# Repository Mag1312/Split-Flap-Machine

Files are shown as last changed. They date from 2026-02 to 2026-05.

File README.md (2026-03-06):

# Split-Flap-Machine

This split flap machine is a hobby project by Mag, It is a device which displays time, date, weekday, weather, any word which is less than 7 letters and can even play your favourite songs from a MicroSD Card.

## Introduction

The Split Flap Machine's main attraction, The split flap consists of 37 flaps, 10 numbers (0-9), 26 alphabets (A-Z) and a blank flap. It is made possible mainly with the use of 28byj48 stepper motor, A4988 driver, Hall sensor and an ESP 32. The split flap drum has a small neodimium magnet which gets detected by the hall sensor and sends an update, the place where the magnet's field is not felt by the sensor, is the 0 position. Whenever something is to be displayed, the drum/spool is rotated with respect to this position to display.

The music system works from the webserver, where there are controls to play music. These controls can be used to play music from the MicroSD card.

This all works on a 10000MaH battery.

## Detailed Explanation

The split flap machine consists of 7 split flap units, consisting of 37 flaps, a spool and a stand. A single split flap unit uses a 28byj48 stepper motor, A4988 stepper driver, ky035 hall sensor and a ball bearing.
As mentioned earlier, after the startup a calibration function runs which runs in the following process.

Rotate spool until magnet detected --> Rotate spool until magnet is not detected --> set position = 0

After which to display a character, it first checks the ascii value of the character to be displayed in a seperate array, the position of the array of the ascii value is taken. the position of array times the number of steps per flap is multiplied to get the required position to revolve to display the character. Afterwhich the motor rotates the spool until the position is achieved. There is a killswitch if the spool rotates more than 1 revolution the program fails and freezes.

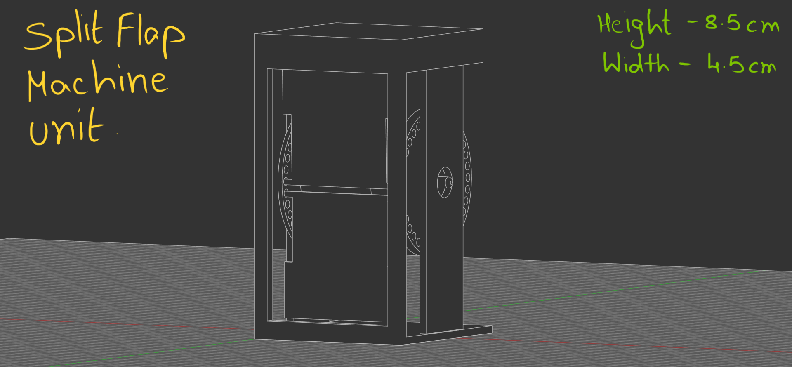
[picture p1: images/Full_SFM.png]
image of a unit of split flap display


You can better understand this in my firmware, go check it out. This is the central operation around which all functions work.

The song system uses a MicroSD card, PCM5102A DAC Module, PAM8406 Amplifier and 2x 8ohm 3Watt speakers. This has been chosen for the highest quality and a mid-high battery life.

The system uses a 10000MaH battery pack with a buck converter to convert voltage.

#

Read Timeline.md for more understanding.

If you have any regards or have found an issue please contact +91 9346651359 (or) email to magazine2512@gmail.com.

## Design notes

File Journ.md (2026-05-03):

---
# Split-Flap-Machine
Author - "Magazine1312/Mag2512/Mag1312"
Descrption - "A Split Flap Machine is a device worthy to display 7 letter words, Weather, Clock, Day, Date etc.. It can even play Music!"
Created - "2026-02-25"
This file focuses on the process of creation of Split Flap Machine as created by Mag (The creator)
---

[Note - The measurements are not mentioned unless specified in the timeline text, It is expected that the reader will download the files to check the measurements]

# Febrauary 25: Created Spool and Flaps for Machine

Created the flaps (Self Explanatory)
Created the Spools (The drums where the flaps are placed for SFM to rotate)
 - The spool has been divided into 2 parts, The part 1 (The top part) and part 2 (The bottom part) [look at the image for better understanding]

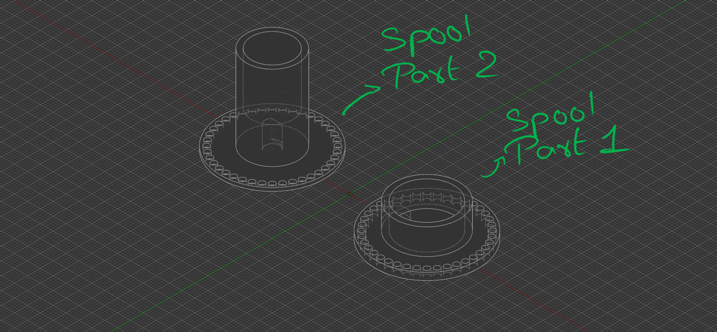
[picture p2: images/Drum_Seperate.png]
Spools


Both the spools have 40 holes, having diameter greater than that of flap ends. The angle between the centres of two circles and the centre of the base of the spool is 9 degrees.

The spools are attached to eachother by inserting Spool 2 into Spool 1. For better understanding, please refer to the image below.

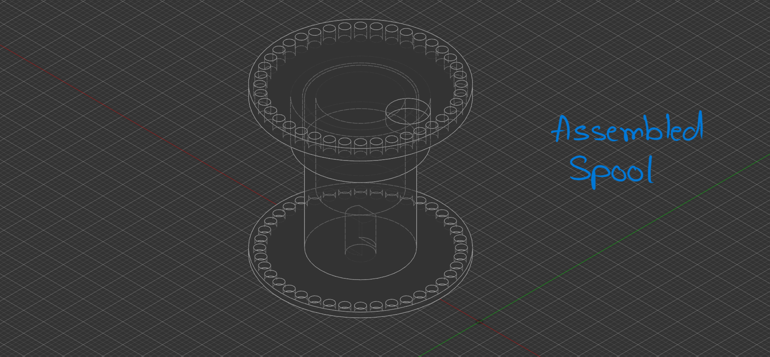
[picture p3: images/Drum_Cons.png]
Image of a constructed spool


The spool 1 has a cavity for holding a Neodymium magnet for the working of Hall sensor which is specified later.
Simillarly spool 2 has a cavity for the Stepper motor's shaft to rotate the spool also specified later.

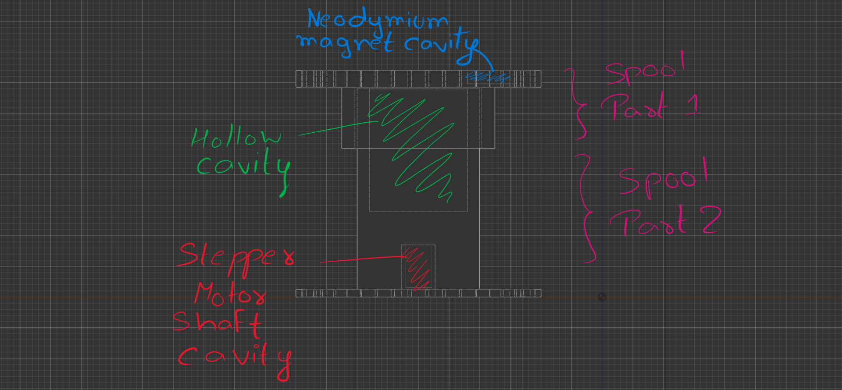
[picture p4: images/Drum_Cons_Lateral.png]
Image of a constructed spool's lateral section


The semi constructed spool with flap is given below, for complexity and space constraints only one flap has been attached.

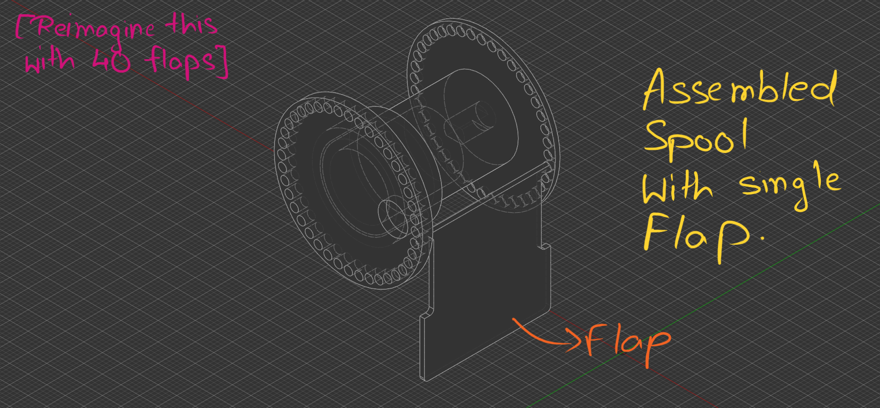
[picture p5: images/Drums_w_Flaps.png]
Image of a constructed spool with a flap attached


**Total Time Spent: 4 hours**

# February 26: Created Spool Holder and updated designs

Created a Spool stand. SPECIFICALLY designed for when the flaps of the spool hit the front part of the stand, it doesnt fall and stays there until there is a 10 degree rotation.

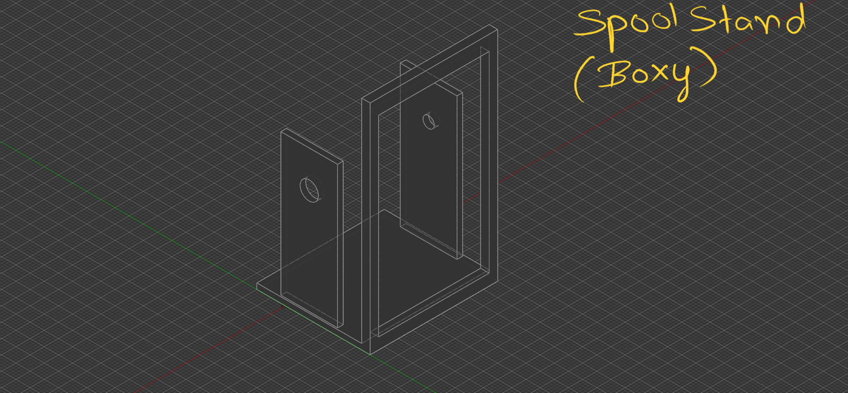
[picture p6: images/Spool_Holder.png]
Image of spool stand


And we got some changes, Since The older spool design with 40 holder was TOO EXPENSIVE (The cost adds up for 7 of them, so its 280 if its 40 holders) so I reduced it to only 36. 26 for letters and 10 for numbers from 0-9.

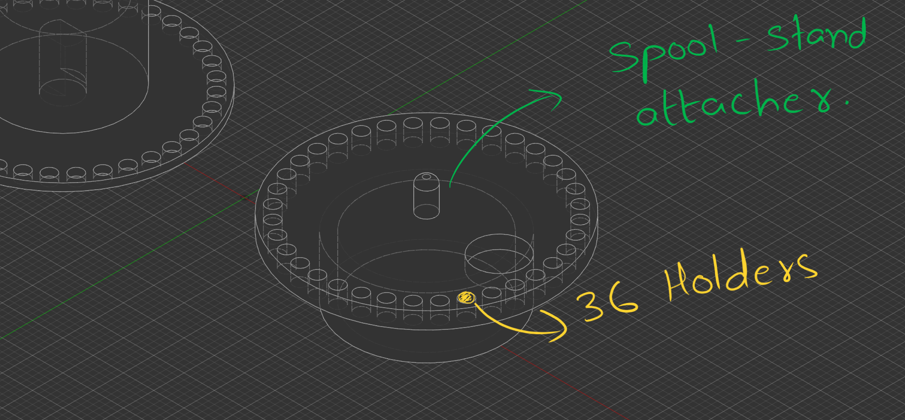
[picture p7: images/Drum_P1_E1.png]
Image of updated spool V1


Here you can see the spool stand attacher, ensuring that it can rotate freely without disorientating.

Welp, its 2am and I've made some changes. 
The spool stand attacher will work however for smooth rotation I have decided to use ball bearings of 3x8x4mm. I had to do multiple revisions and changes for the somewhat final SFM unit.
firstly I added a cavity for ball bearing as mentioned. Next I made the height of the SFM unit around 8.5cm and also had to add an offset slab which stops the top flap from falling down unless turned 10 degress. (See the image)
and next I updated the overall look of the Stand it looks more boxier and it was the design I was going for.

1.5 hrs of work

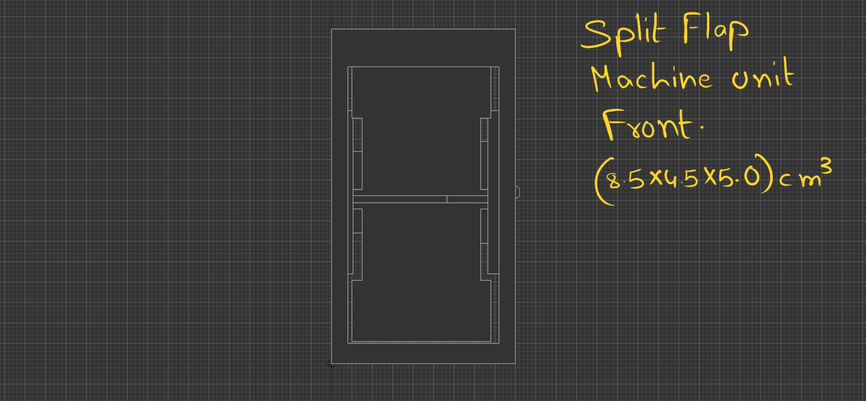
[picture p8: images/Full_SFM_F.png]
another one


**Total Time Spent: 3 hours**

# February 27: Updated Spool Stand Design and made a BOM list

As soon as I woke up I made a cavity in the Spool Holder for a screw so that when the flaps fall they make the sound which we want to hear and also makes the flaps not swing after falling down (This is the major cause).

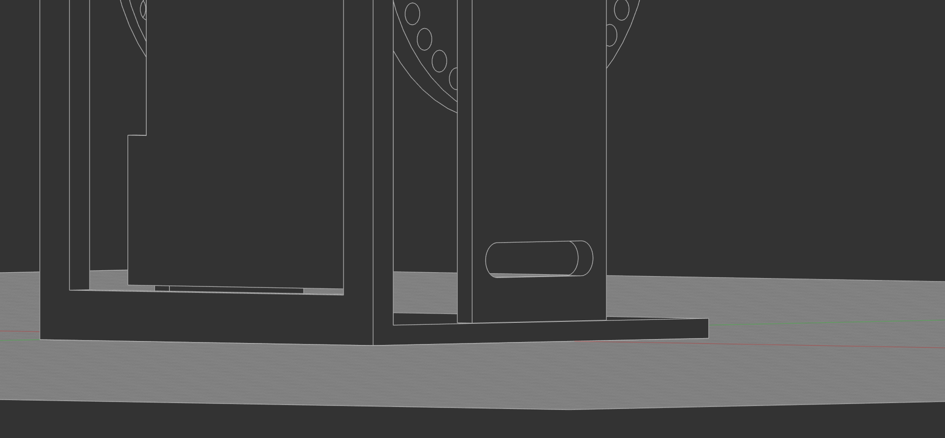
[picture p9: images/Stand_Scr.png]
Spool Stand Screw Cavity


Next Since the design was nearly final I made a BOM list although I Have not decided yet how to power this so I have not included any power supply or things which are used to power this (I have to Research). And the total cost of the machine comes to nearly 97$, A whole lot of expensive, Major cost includes 3d printing service, filament and Arduino Nano. Well 3d printing in my local is much cheaper than online service which is charging, 110$ JUST FOR THE FLAPS OF 7 UNITS! In the price of flaps I can print my whole machine locally, However I doubt blueprint will give me funds to convert credit into real money so I can pay the local service so I doubt it.

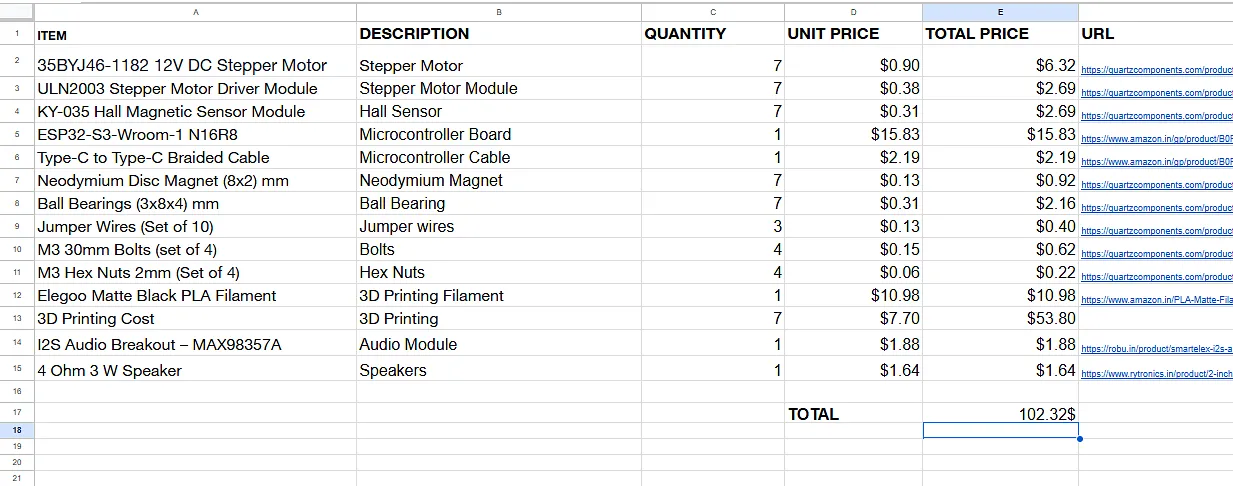
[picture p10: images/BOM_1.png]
BOM


**Total Time Spent: 3 hours**

# March 1: Made code to calibrate the machine

This day was brainfoggy one, I had no idea how to code the script and I had to go through multiple videos of how arduino's control stepper motors, haul sensor and in basic the whole setup (the code is same for arduino and esp32). Even after all this, I was still not able to find what to do so I asked chatGPT and it asked me to follow a path. I had the map and was on my own, testing logics and all. I worked on calibration today, What it does is that everytime the SFM starts up, it doesnt know which letter it is displaying so in the calibration it slowly rotates the spool and uses the hall sensor to detect the magnet, when the magnet is in close contact to the hall sensor the hall sensor reads LOW and vice versa. So this calibration is only right when the hall sensor first reads HIGH then LOW then HIGH and the point where hall sensor transitions from LOW to HIGH is the point of 0 position and all characters are labelled relative to this position.

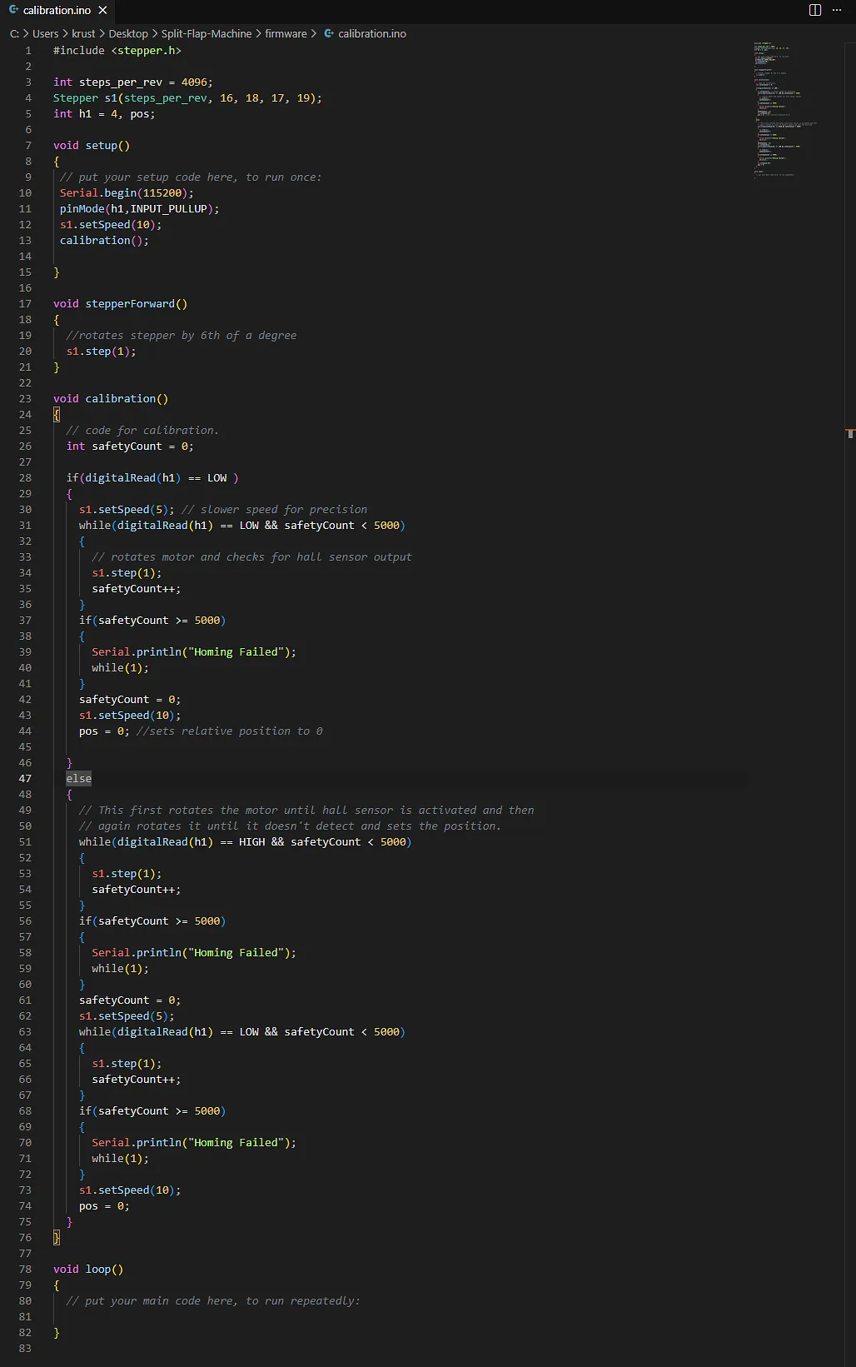
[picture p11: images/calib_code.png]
code of calibration


**Total Time Spent: 4 hours**

# March 4: Made code to connect ESP 32 to the internet to get data like time

Today I made a code to fetch time from the internet (watch this video for info : https://youtu.be/9OcewS8sa68?si=-juCJv46duffQA7_). And I also updated the BOM list because with only 1 esp 32, I would be falling short of gpio pins for the motors and other features, So I had two options either use a gpio extension board or buy another esp 32. After painfully reading the advantages and disadvantages of both, it was quite clear that another esp 32 is the best option so I did  so!

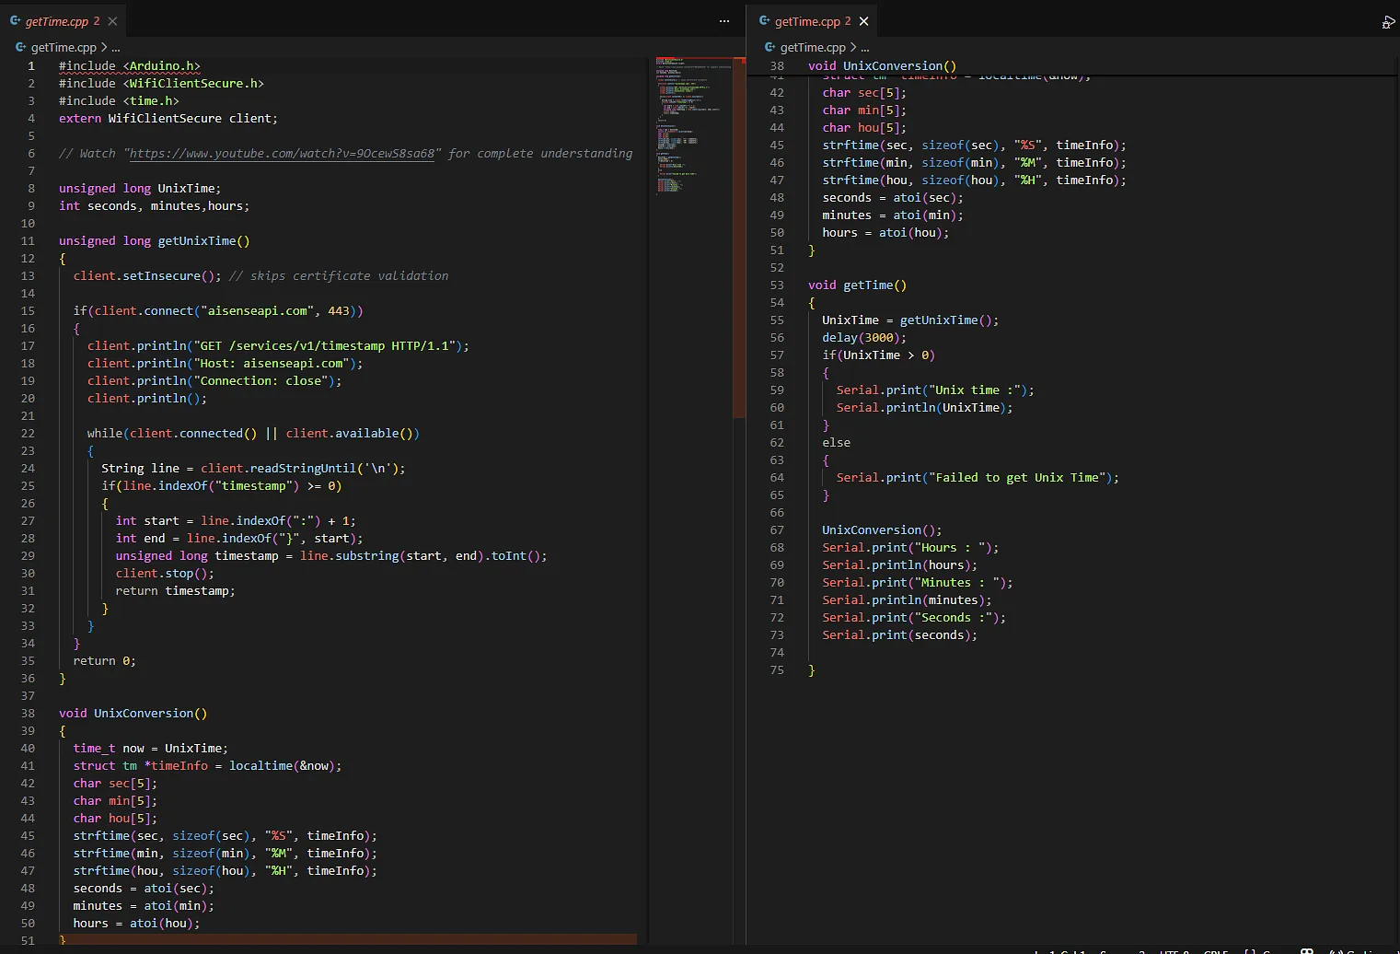
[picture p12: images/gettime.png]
code of getTime function


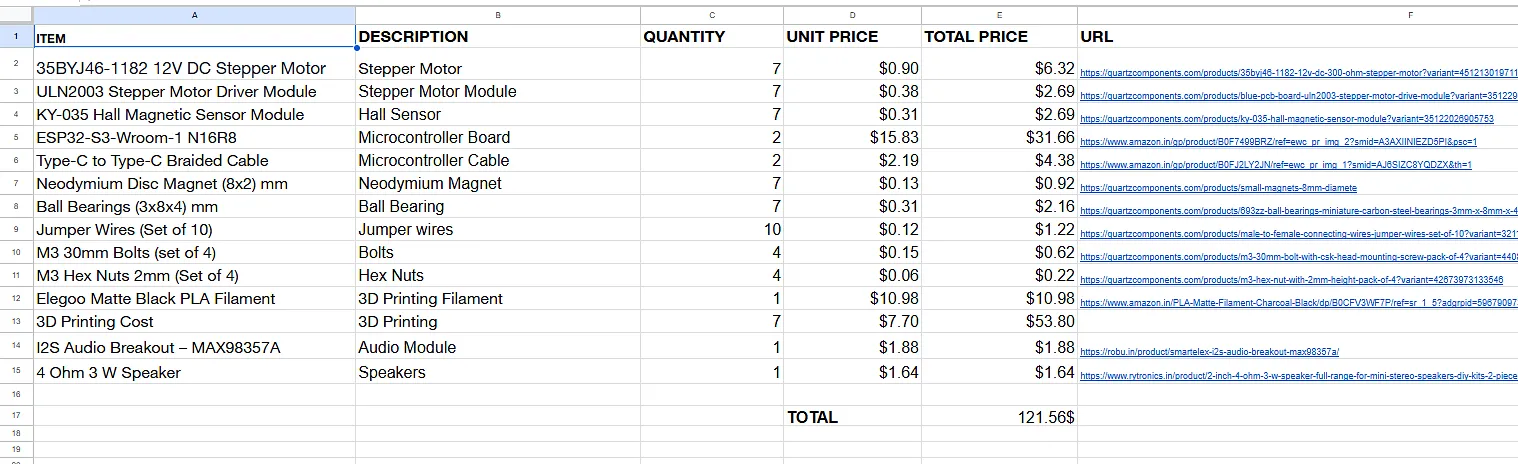
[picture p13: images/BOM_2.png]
BOM LIST 2


**Total Time Spent: 5 hours**

# March 5: I made code to calibrate all units at once

In todays episode of Split Flap Device, I made a code for all the 7 units of the device to calibrate at once!

This is achieved by calling the setupCalibration() function from the main .ide file. This function then called the fullCalibration() function.

Here's a simple explanation of the full calibration function - First the hall sensors output is detected if it is on the magnet or near its magnetic field, it goes in the first if block, in it one motor is rotated by 1 step and then it is checked if the hall sensors output has changed, if not it goes to the setupCalibration() function and in the loop follows fullCalibration() function again for another stepper motor.

This process might seem lengthy but to the human eye it seems as if all the 7 units are being calibrated at once! The delay between 2 fullCalibration() functions is so small that it is not noticable!

Props to Chatgpt for letting me know this process, It was quite interesting and very understandable and I was able to code without any help of chatGPT using my own skills!

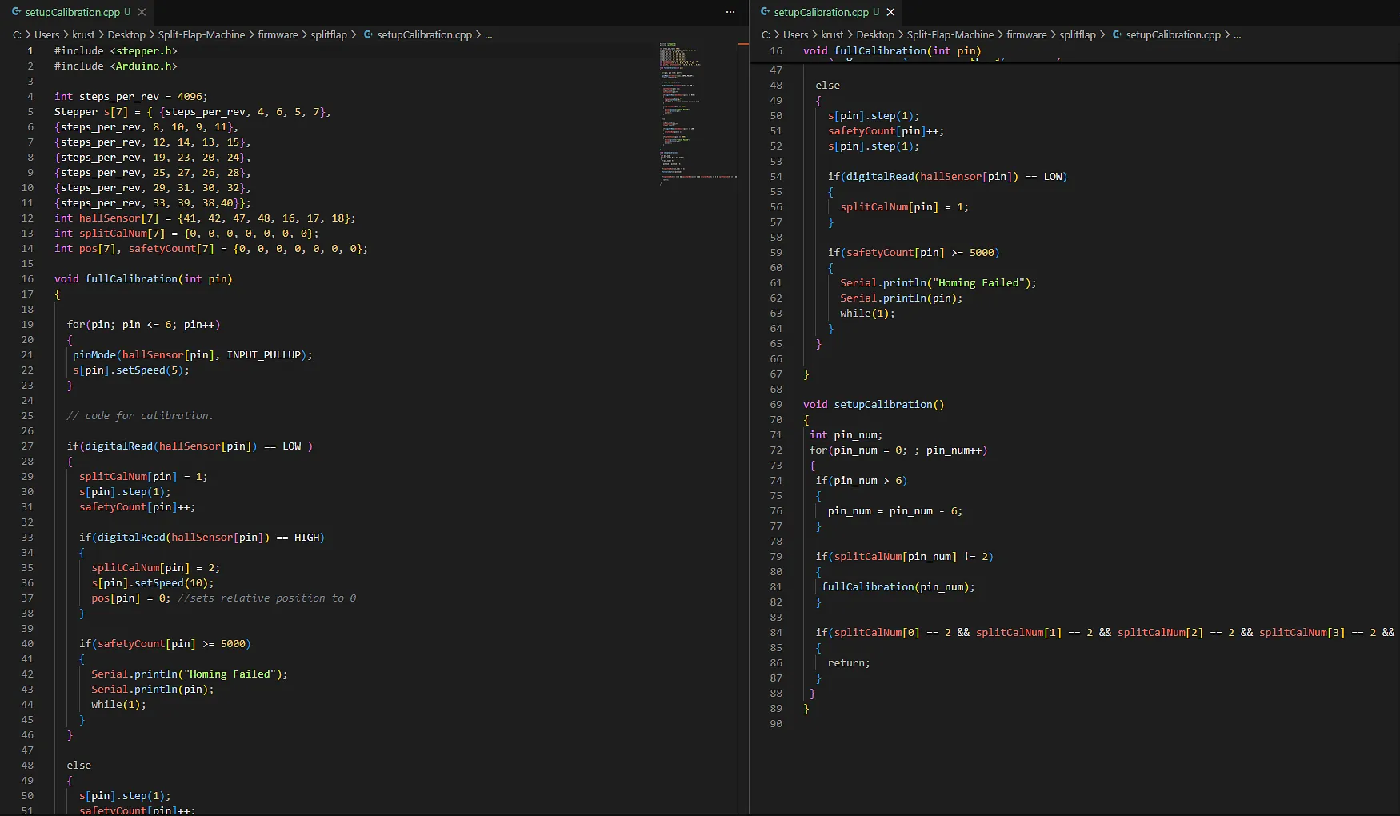
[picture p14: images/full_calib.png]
code of full calibration


**Total Time Spent: 4 hours**

# March 6: Made code to display Time, Date, Weather, Day

This was one of the most productive days.

Today I made a program to display time, date, weather, weekday on my split flap device!

Inshort today was a day of arduino ide, It took a lot of time, approximately 6 hours for all these but it was worth it!

the displaying works on the following principle -
It first arranges the words to be displayed in a character array and compares it with ascii values, if it matches it goes on an gets a position which is calculated so that only that letters position is sent. Next the motors rotate one by one by 1 step until all of they reach their final position.

This is the basic program and is used in all 4 of my programs. The weather program however uses api to get its data from the internet through esp 32s wifi feature.

Thats it for today, tommorrows plan is to make a webserver for esp32 and make a program so that when a word is entered in the webserver it is displayed on the split flap machine.

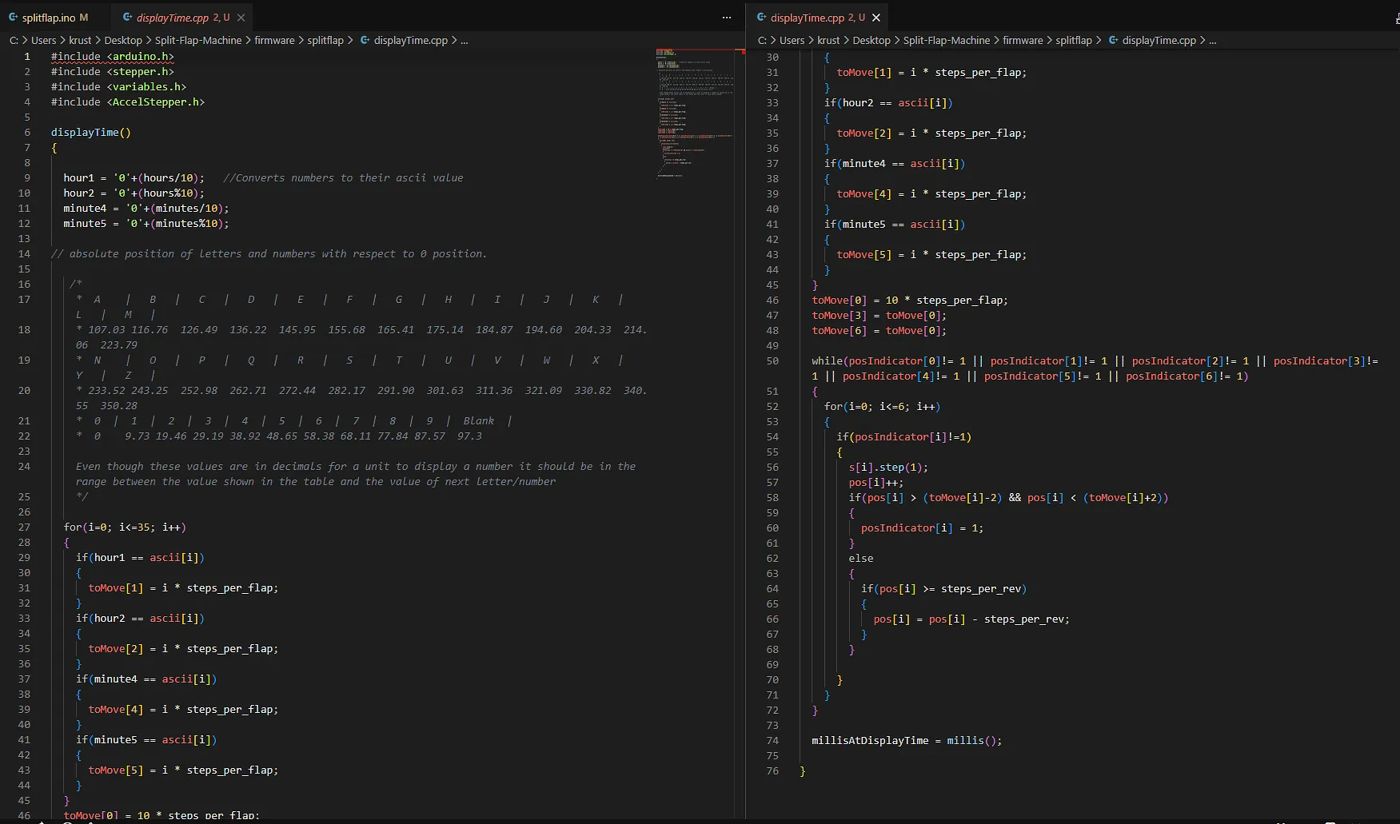
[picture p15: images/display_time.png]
code of display time


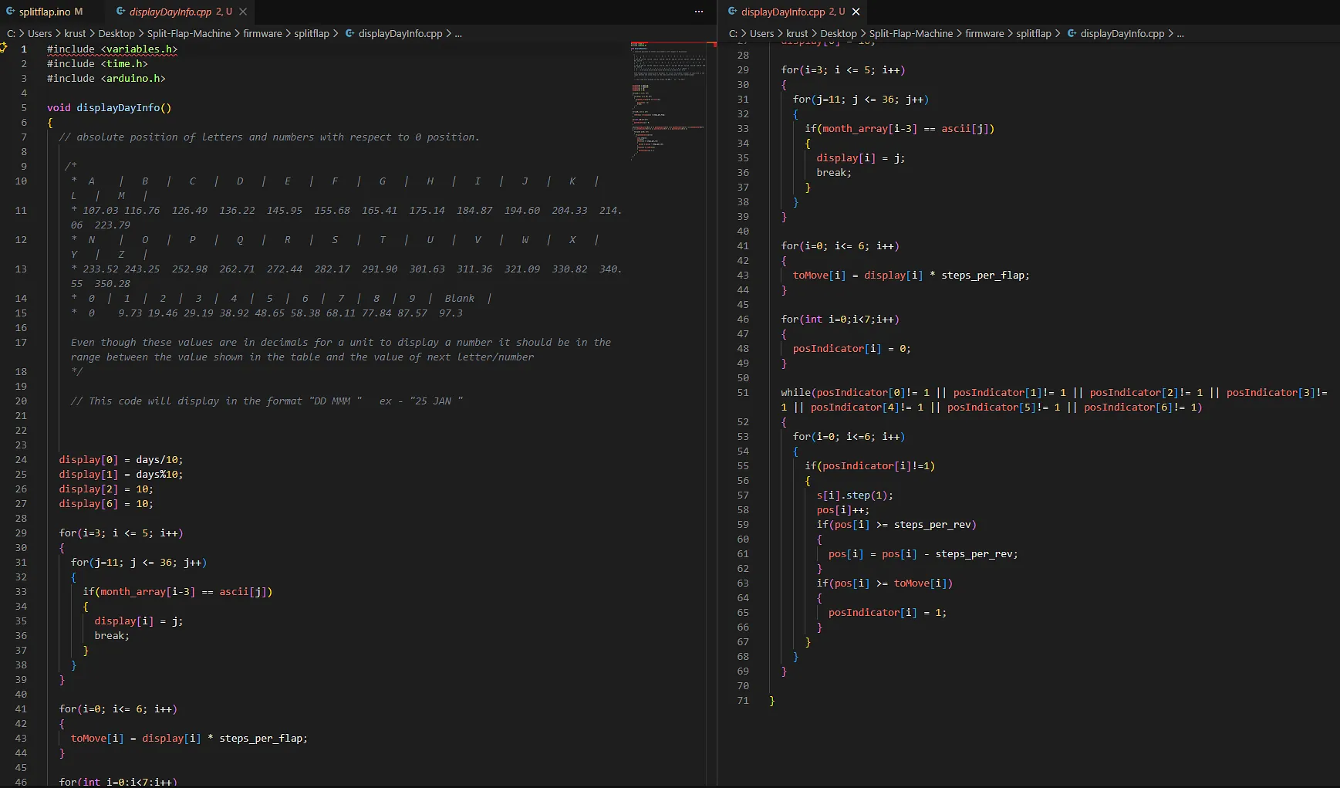
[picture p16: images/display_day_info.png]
code of display date


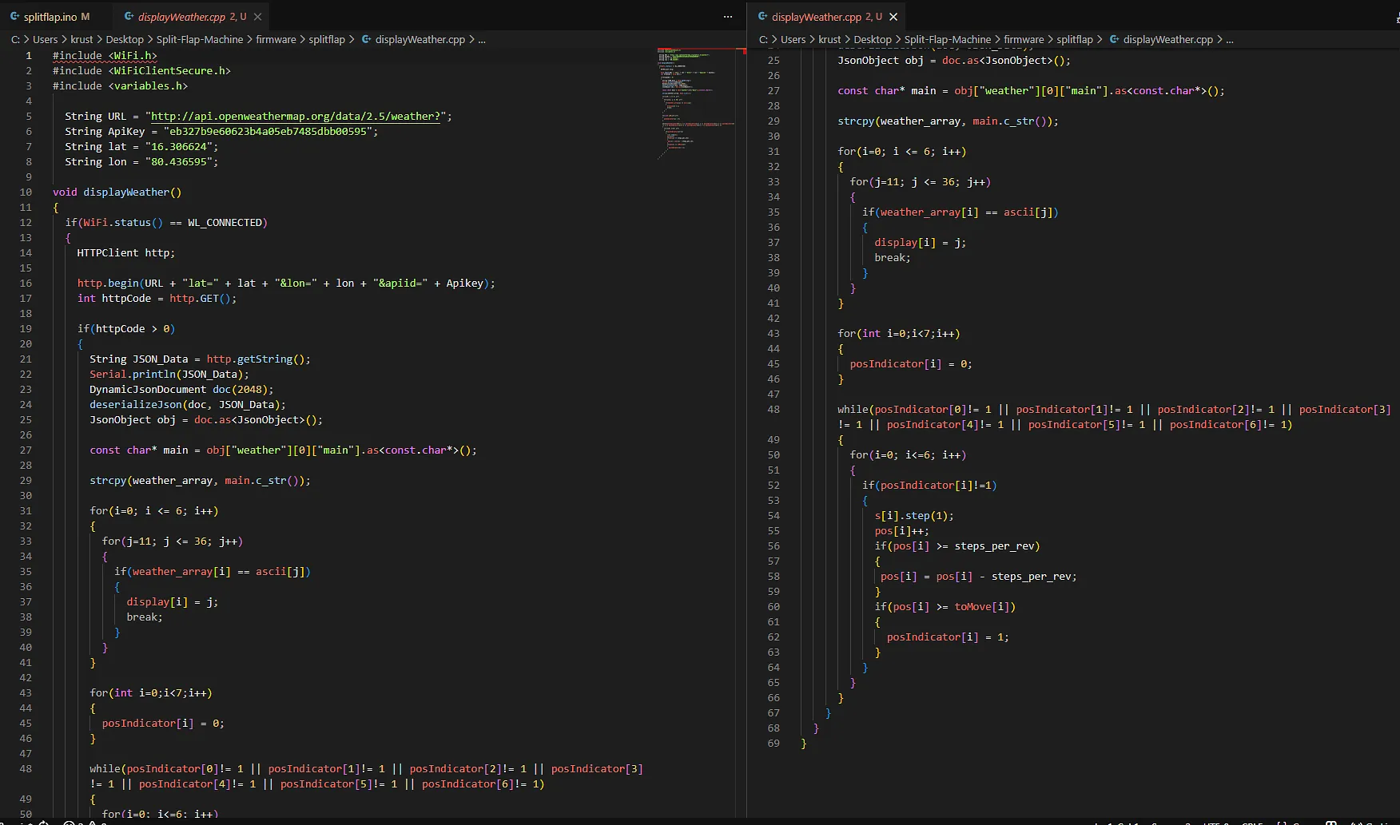
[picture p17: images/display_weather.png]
code of display weather


**Total Time Spent: 6 hours**

# March 7: Completed the software part and made a final BOM list

Today was the day where the software part was completed!

In todays episode of Split Flap Display, I created a webserver having the functionality so that one can control the split flap machine from their phone, It also has song playback feature. This is achieved through UART communication between 2 ESP32s, which uses an MicroSD card to store all the songs. 

This could be updated to a streaming playback in the future, which is a matter of only few code lines.

I also updated the final BOM list for Hackclub's design review and funds allocation.

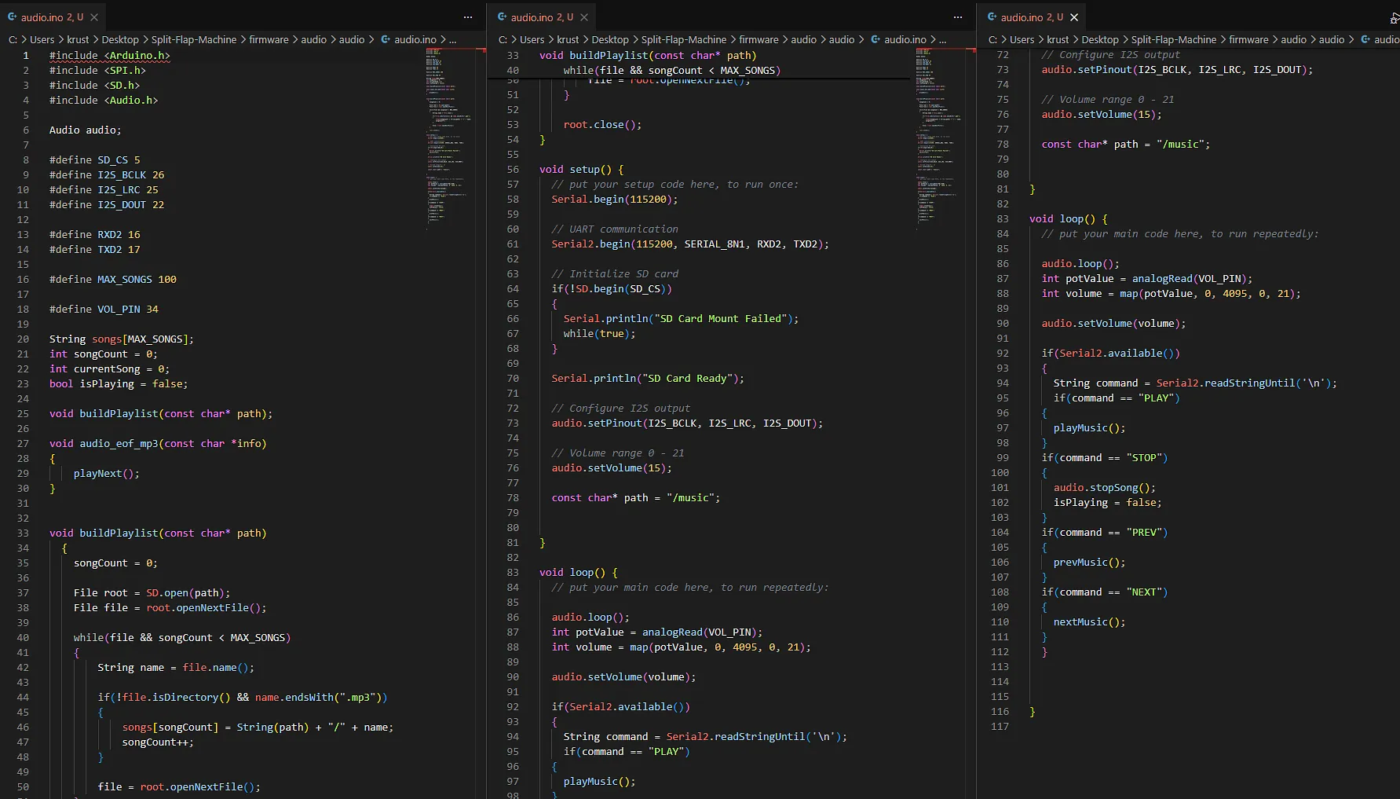
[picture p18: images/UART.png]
code of audio


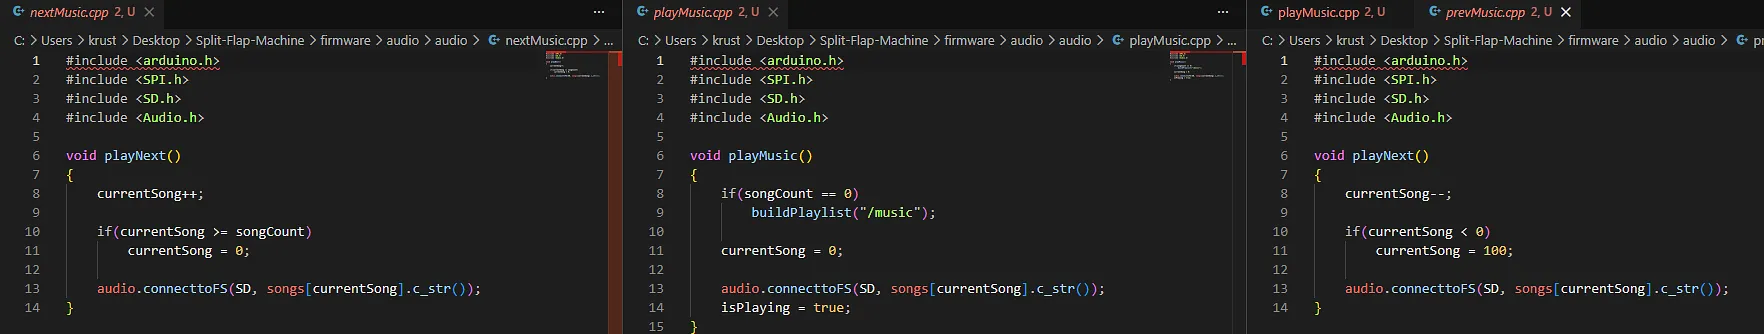
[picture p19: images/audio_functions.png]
code of audio2


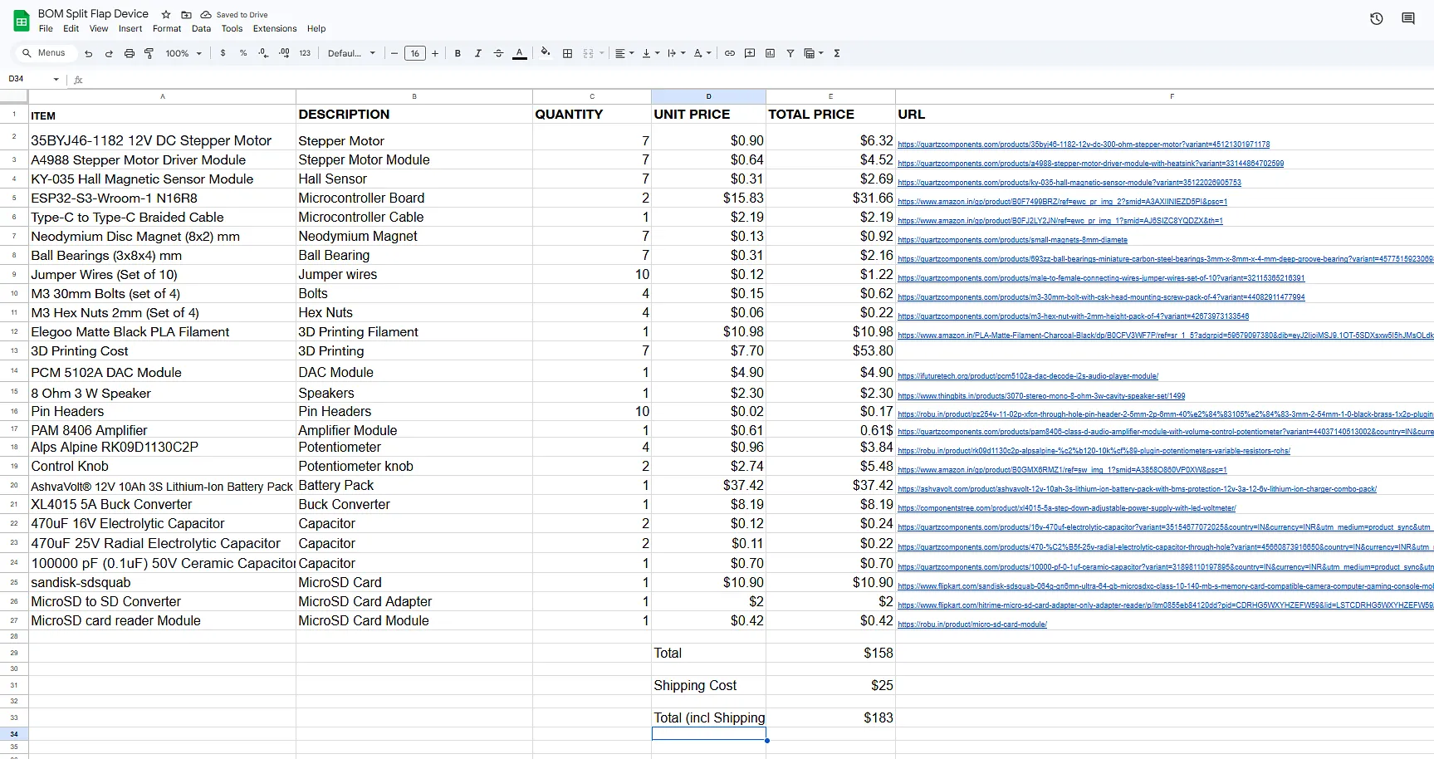
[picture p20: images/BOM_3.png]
BOM LIST


And Hence today I submit the design review and hopefully it goes clear.

**Total Time Spent: 6 hours**

#

**Time Spent on Project: 35 hours**

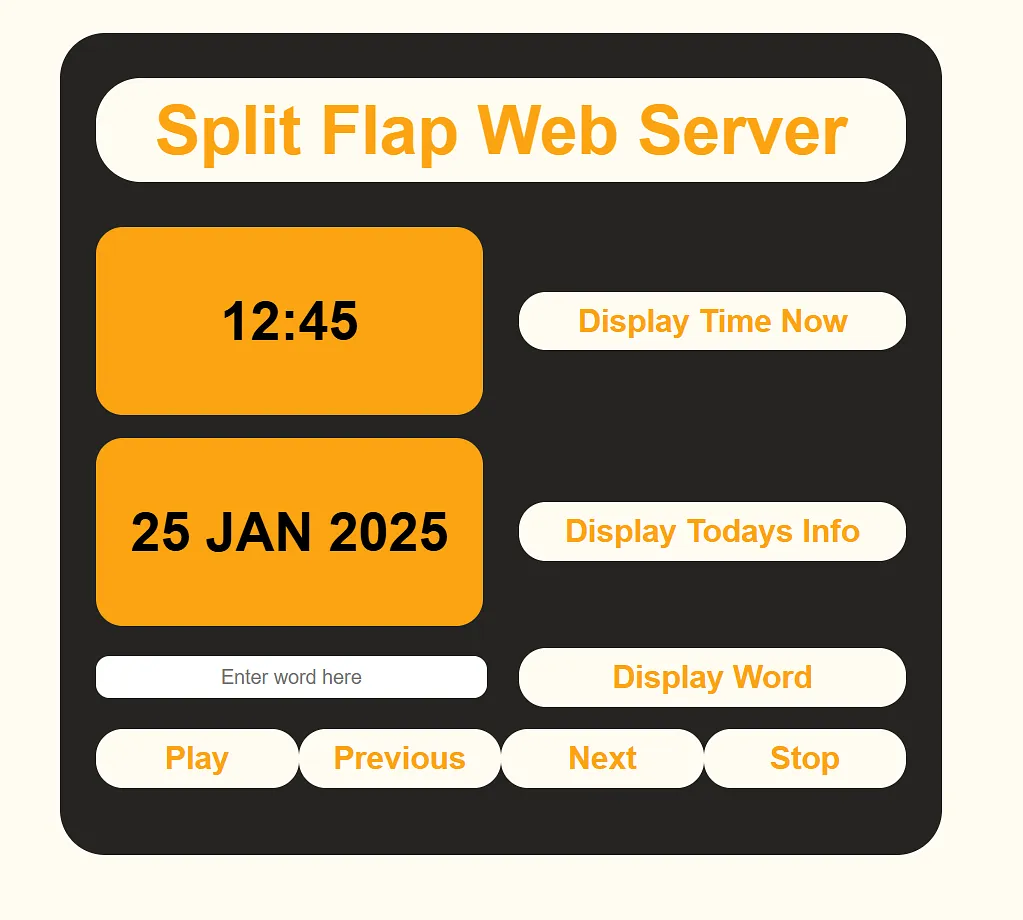
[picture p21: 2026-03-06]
images/Web_server.png

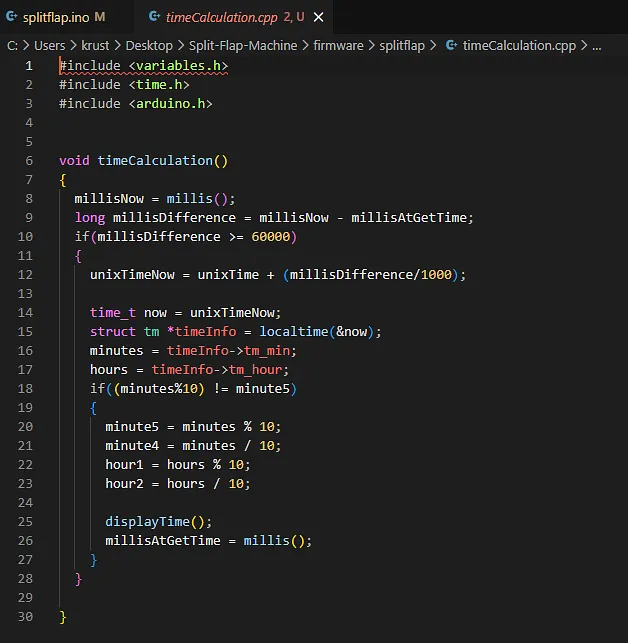
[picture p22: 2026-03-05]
images/time_calculation.png

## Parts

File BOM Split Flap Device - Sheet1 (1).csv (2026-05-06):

ITEMS | DESCRIPTION | QUANTITY | UNIT PRICE | TOTAL PRICE | URL | OTHER INFO
28BYJ48 5V DC Stepper Motor | Stepper Motor | 7 | $0.97 | $6.70 | https://robu.in/product/28byj-48-stepper-motor-dc-5v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
A4988 Stepper Motor Driver Module | Stepper Motor Module | 7 | $0.76 | $5.34 | https://quartzcomponents.com/products/a4988-stepper-motor-driver-module-with-heatsink?variant=33144864702599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
KY-035 Hall Magnetic Sensor Module | Hall Sensor | 7 | $0.21 | $1.48 | https://quartzcomponents.com/products/ky003-hall-effect-magnetic-sensor?variant=39261093134520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
ESP32-S3-Wroom-1 N16R8 | Microcontroller Board | 2 | $10.58 | $21.16 | https://www.amazon.in/LAND-INDIA-ESP32-Development-Microcontroller/dp/B0FG3BBKPH
Type-C to Type-C Braided Cable | Microcontroller Cable | 1 | $2.19 | $2.19 | https://www.amazon.in/gp/product/B0FJ2LY2JN/ref=ewc_pr_img_1?smid=AJ6SIZC8YQDZX&th=1
Neodymium Disc Magnet (8x2) mm | Neodymium Magnet | 7 | $4.52 | $4.52 | https://www.flipkart.com/jinsa-50pcs-dia-8x2mm-round-disc-neodymium-rare-earth-magents-art-crafts-multipurpose-office-magnets-pack-50/p/itm078c0c0845b31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
Ball Bearings (3x8x4) mm | Ball Bearing | 7 | $0.31 | $2.16 | https://quartzcomponents.com/products/693zz-ball-bearings-miniature-carbon-steel-bearings-3mm-x-8mm-x-4-mm-deep-groove-bearing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
M3 30mm Bolts (set of 4) | Bolts | 4 | $0.15 | $0.62 | https://quartzcomponents.com/products/m3-30mm-bolt-with-csk-head-mounting-screw-pack-of-4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
M3 Hex Nuts 2mm (Set of 4) | Hex Nuts | 4 | $0.06 | $0.22 | https://quartzcomponents.com/products/m3-hex-nut-with-2mm-height-pack-of-4?variant=42673973133546
Female Headers (2 pin) | Pin Headers | 50 | $0.08 | $4.21 | https://robu.in/product/fh1-27-01-02pzd-xunpu-plugin1x2-pin-1-27mm-female-headers-rohs/
Female Headers (3 pin) | Pin Headers | 10 | $0.08 | $0.90 | https://robu.in/product/fh1-0-01-03pzd-xunpu-plugin1x3-pin-1mm-female-headers-rohs/
PCM 5102A DAC Module | DAC Module | 1 | $4.90 | $4.90 | https://ifuturetech.org/product/pcm5102a-dac-decode-i2s-audio-player-module/
8 Ohm 5 W Speaker | Speakers | 1 | $3.16 | $3.16 | https://thinkrobotics.com/products/2030-cavity-speaker-8%CF%89-2w?variant=49309283025213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
Pin Headers | Pin Headers | 10 | $0.02 | $0.17 | https://robu.in/product/pz254v-11-02p-xfcn-through-hole-pin-header-2-5mm-2p-6mm-40%e2%84%83105%e2%84%83-3mm-2-54mm-1-0-black-brass-1x2p-pluginp2-54mm-pin-head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
PAM 8406 Amplifier | Amplifier Module | 1 | $0.61 | 0.61$ | https://quartzcomponents.com/products/pam8406-class-d-audio-amplifier-module-with-volume-control-potentiometer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
Alps Alpine RK09D1130C2P | Potentiometer | 4 | $0.96 | $3.84 | https://robu.in/product/rk09d1130c2p-alpsalpine-%c2%b120-10k%cf%89-plugin-potentiometers-variable-resistors-rohs/
Control Knob | Potentiometer knob | 2 | $2.74 | $5.48 | https://www.amazon.in/gp/product/B0GMX6RMZ1/ref=sw_img_1?smid=A3858O860VP0XW&psc=1
AshvaVolt® 12V 10Ah 3S Lithium-Ion Battery Pack | Battery Pack | 1 | $37.42 | $37.42 | https://ashvavolt.com/product/ashvavolt-12v-10ah-3s-lithium-ion-battery-pack-with-bms-protection-12v-3a-12-6v-lithium-ion-charger-combo-pack/
XL4015 5A Buck Converter | Buck Converter | 1 | $7.89 | $7.89 | https://robu.in/product/xl4015-5a-dc-dc-step-adjustable-power-supply-buck-module-led-w-voltmeter/?gad_source=1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
0.1uF Ceramic Capacitor | Capacitor | 30 | $0.06 | $1.91 | https://quartzcomponents.com/products/10000-pf-0-1uf-ceramic-capacitor?variant=31898110197895
470uF 50V Electrolytic Capacitor | Capacitor | 1 | $0.07 | $0.07 | https://quartzcomponents.com/products/470uf-50v-electrolytic-capacitor
47uF 10V Electrolytic Capacitor | Capacitor | 2 | $0.04 | $0.08 | https://quartzcomponents.com/products/47uf-10v-electrolytic-capacitor
100uF 16V Electrolytic Capacitor | Capacitor | 10 | $0.03 | $0.35 | https://quartzcomponents.com/products/6v-100uf-electrolytic-capacitor
100uF 25V Electrolytic Capacitor | Capacitor | 10 | $0.03 | $0.35 | https://quartzcomponents.com/products/100uf-25v-radial-electrolytic-capacitor
1000uF 16V Electrolytic Capacitor | Capacitor | 2 | $0.08 | $0.20 | https://quartzcomponents.com/products/1000uf-16v-aluminum-electrolytic-capacitors-leaded
sandisk-sdsquab | MicroSD Card | 1 | $16.83 | $16.83 | https://www.flipkart.com/sandisk-sdsquab-064g-gn6mn-ultra-64-gb-microsdxc-class-10-140-mb-s-memory-card-compatible-camera-computer-gaming-console-mobile-table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
MicroSD to SD Converter | MicroSD Card Adapter | 1 | $3 | $3 | https://www.flipkart.com/carecase-pack-3-sam-sung-micro-sd-adapter-compatible-all-mobile-memory-cards-card-reader/p/itmc5f69c3882c43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
MicroSD card reader Module | MicroSD Card Module | 1 | $0.42 | $0.42 | https://robu.in/product/micro-sd-card-module/
9x15cm Perf Board | Perf Board (PCB) | 2 | $0.98 | $2 | https://robu.in/product/9-x-15-cm-universal-pcb-prototype-board-single-sided-2-54mm-hole-pitch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
4x6cm Perf Board | Perf Board (PCB) | 1 | $1 | $1 | https://robu.in/product/5-x-7-cm-universal-pcb-prototype-board-single-sided-2-54mm-hole-pitch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
Pin Headers (2 Pin) | Pin Headers | 30 | $0.03 | $1 | https://robu.in/product/ph1-0-01-02pzd-xunpu-plugin1x2-pin-1mm-pin-headers-rohs/
Pin Headers (3 Pin) | Pin Headers | 10 | $0.03 | $1 | https://robu.in/product/ph1-27-01-03pzd-xunpu-plugin1x3-pin-1-27mm-pin-headers-rohs/
Jumper Wires (20 cm) | Jumper Wires | 1 | $0.46 | $0.46 | https://robu.in/product/male-to-female-jumper-wires-40pcs-20cm/
18AWG (RED) | Wires | 1 | $0.34 | $0.34 | https://robu.in/product/18awg-high-voltage-silicone-wire-3000v-red/
18AWG (BLACK) | Wires | 1 | $0.34 | $0.34 | https://robu.in/product/18awg-high-voltage-silicone-wire-3000v-black/
20AWG (RED) | Wires | 2 | $0.16 | $0.32 | https://robu.in/product/ul1007-20awg-pvc-electronic-wire-red/
20AWG (BLACK) | Wires | 2 | $0.16 | $0.32 | https://robu.in/product/ul1007-20awg-pvc-electronic-wire-black/
22AWG (RED) | Wires | 2 | $0.16 | $0.32 | https://robu.in/product/22awg-silicone-braided-wire-red/
22AWG (BLACK) | Wires | 2 | $0.16 | $0.32 | https://robu.in/product/22awg-silicone-braided-wire-black/
26AWG (RED) | Wires | 2 | $0.08 | $0.16 | https://robu.in/product/high-quality-ultra-flexible-26awg-silicone-wire-1000m-red/
26AWG (BLACK) | Wires | 2 | $0.08 | $0.16 | https://robu.in/product/ul1007-26awg-pvc-electronic-wire-black/
Wire Stripper | Wire Stripper | 1 | $2.55 | $2.55 | https://robu.in/product/multitec-02dx-self-adjusting-wire-cutter-stripper/
Helping Hands | Helping Hands | 1 | $9.40 | $9.40 | https://www.amazon.in/gp/product/B0DFQ6G523/ref=ewc_pr_img_1?smid=A3T8K809Q96RB6&psc=1
Solder Wick | Solder Wick | 1 | $0.70 | $0.70 | https://robu.in/product/best-quality-solder-desoldering-wire-de-soldering-wick/
 |  |  | TOTAL - | $156.23
 |  |  | TOTAL (incl Shipping) - | $180

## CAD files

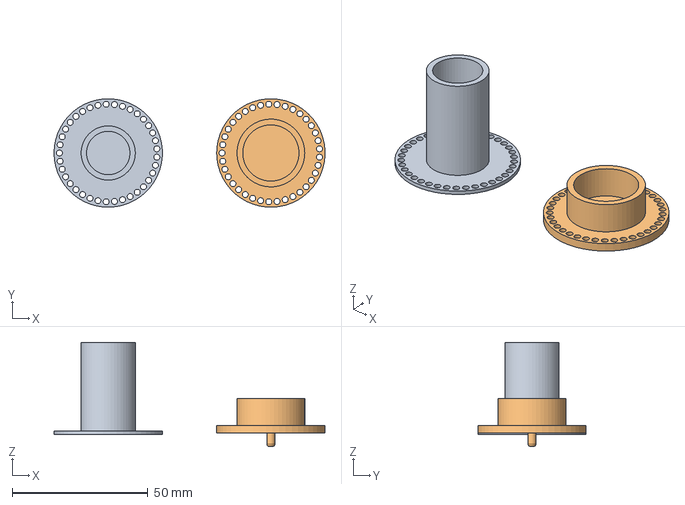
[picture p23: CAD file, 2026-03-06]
CAD STEP/Drum.stp
100.0 x 40.0 x 38.5 mm

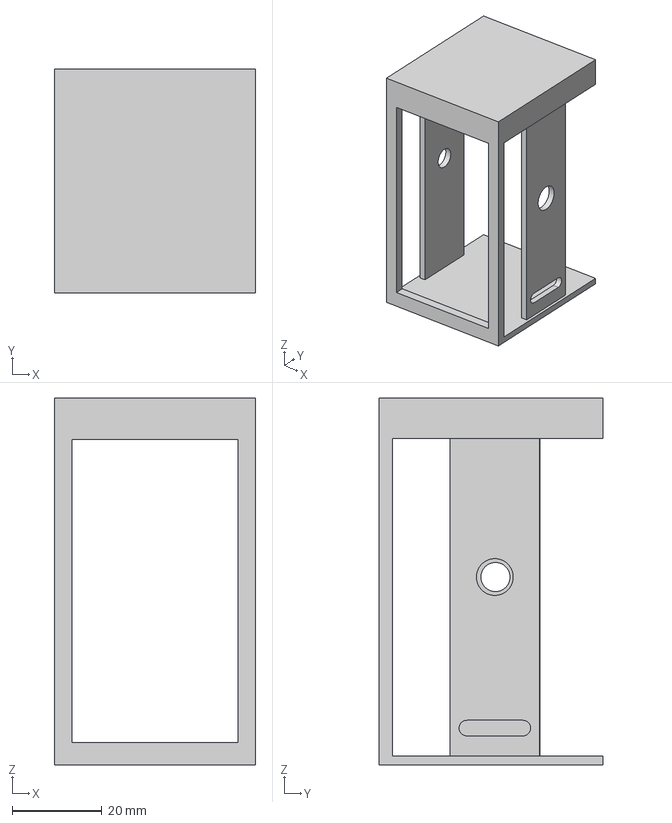
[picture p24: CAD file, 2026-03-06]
CAD STEP/Spool+Stand.stp
45.0 x 50.0 x 82.0 mm

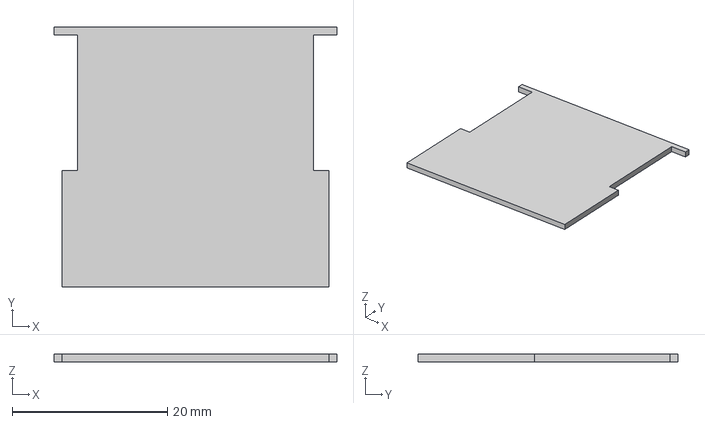
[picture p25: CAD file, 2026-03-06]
CAD STEP/Flaps.stp
36.5 x 33.5 x 1.00 mm

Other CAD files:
CAD/Drum.f3d
CAD/Flaps.f3d
CAD/Spool Stand.f3d

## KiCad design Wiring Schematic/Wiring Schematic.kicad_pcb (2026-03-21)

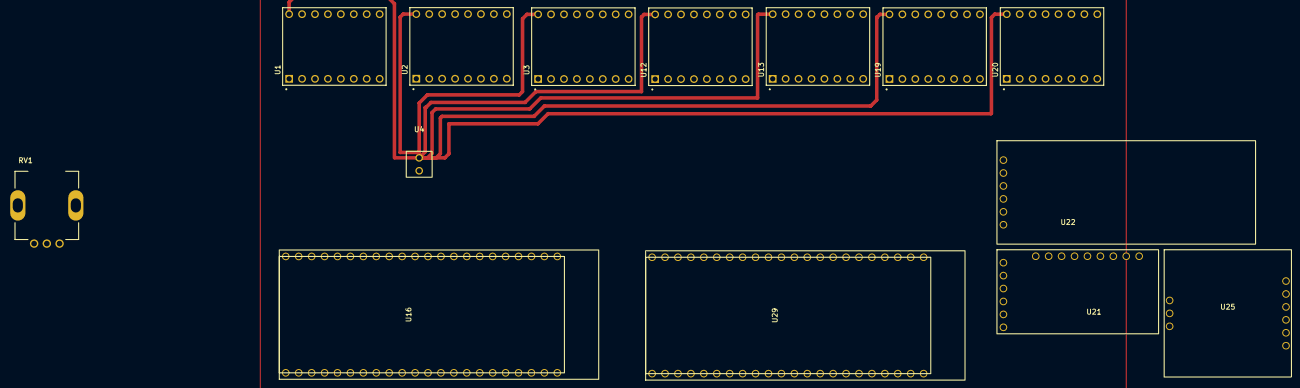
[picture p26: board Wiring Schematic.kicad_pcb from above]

Board: 2 copper layers, 14 parts (0 on the bottom side), 29 nets.

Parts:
RV1: R_Potentiometer; XDCR_PEC11R-4215F-S0024
U1, U2, U3, U12, U13, U19, U20: MODULE_A4988_STEPPER_MOTOR_DRIVER_CARRIER
U4: Buck_Converter
U16, U29: ESP 32 S3 Devkit C1
U21: PCM5102A_DAC
U22: MicroSD_Module
U25: PAM_8406

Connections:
+3.3V: RV1.3, U1.RST (RESET), U1.VDD, U2.RST (RESET), U2.VDD, U3.RST (RESET), U3.VDD, U12.RST (RESET), U12.VDD, U13.RST (RESET), U13.VDD, U16.3V3, U19.RST (RESET), U19.VDD, U20.RST (RESET), U20.VDD, U21.VIN, U22.VCC, U29.3V3
+5V: U1.VMOT, U2.VMOT, U3.VMOT, U4.P_OUT(+), U12.VMOT, U13.VMOT, U16.5V (5V0), U19.VMOT, U20.VMOT, U25.VCC, U29.5V (5V0)
GND: RV1.1, U1.MS1, U1.MS2, U1.MS3, U2.MS1, U2.MS2, U2.MS3, U3.MS1, U3.MS2, U3.MS3, U4.P_OUT(-), U12.MS1, U12.MS2, U12.MS3, U13.MS1, U13.MS2, U13.MS3, U16.G (GND), U19.MS1, U19.MS2, U19.MS3, U20.MS1, U20.MS2, U20.MS3, U25.G (GND), U29.G (GND)
GPIO2 - ENB: U1.EN (ENABLE), U2.EN (ENABLE), U3.EN (ENABLE), U12.EN (ENABLE), U13.EN (ENABLE), U19.EN (ENABLE), U20.EN (ENABLE), U29.2 (GPIO2)
GPIO3 - SLP: U1.SLP (SLEEP), U2.SLP (SLEEP), U3.SLP (SLEEP), U12.SLP (SLEEP), U13.SLP (SLEEP), U19.SLP (SLEEP), U20.SLP (SLEEP), U29.3 (GPIO3)
GPIO4 - POT: RV1.2, U16.4 (GPIO4)
GPIO4 - S1: U1.STEP, U29.4 (GPIO4)
GPIO5 - D1: U1.DIR, U29.5 (GPIO5)
GPIO6 - BCK: U16.6 (GPIO6), U21.BCK
GPIO6 - S2: U12.STEP, U29.6 (GPIO6)
GPIO7 - D2: U12.DIR, U29.7 (GPIO7)
GPIO7 - LCK: U16.7 (GPIO7), U21.LCRK
GPIO8 - DIN: U16.8 (GPIO8), U21.DIN
GPIO8 - S3: U19.STEP, U29.8 (GPIO8)
GPIO9 - D3: U19.DIR, U29.9 (GPIO9)
GPIO10 - CS: U16.10 (GPIO10), U22.CS
GPIO10 - S4: U2.STEP, U29.10 (GPIO10)
GPIO11 - D4: U2.DIR, U29.11 (GPIO11)
GPIO11 - MOSI: U16.11 (GPIO11), U22.MOSI
GPIO12 - S5: U13.STEP, U29.12 (GPIO12)
GPIO12 - SCK: U16.12 (GPIO12), U22.SCK
GPIO13 - D5: U13.DIR, U29.13 (GPIO13)
GPIO13 - MISO: U16.13 (GPIO13), U22.MISO
GPIO14 - S6: U20.STEP, U29.14 (GPIO14)
GPIO15 - D6: U20.DIR, U29.15 (GPIO15)
GPIO16 - S7: U3.STEP, U29.16 (GPIO16)
GPIO17 - D7: U3.DIR, U29.17 (GPIO17)
LOUT- LIN: U21.LROUT, U25.LIN
ROUT - RIN: U21.ROUT, U25.RIN

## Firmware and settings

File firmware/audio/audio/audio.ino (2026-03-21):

#include <Arduino.h>
#include <SPI.h>
#include <SD.h>
#include <Audio.h>

Audio audio;

#define SD_CS 5
#define I2S_BCLK 6
#define I2S_LRC 7
#define I2S_DOUT 8

#define RXD2 16
#define TXD2 17

#define MAX_SONGS 100

#define VOL_PIN 34

#define POT_PIN 4   // your ADC pin

float smoothed = 0.0;
float alpha = 0.1;   // smoothing (0.05–0.2 is good)
  

String songs[MAX_SONGS];
int songCount = 0;
int currentSong = 0;
bool isPlaying = false;

void buildPlaylist(const char* path);

void audio_eof_mp3(const char *info)
{
    playNext();
}


void buildPlaylist(const char* path)
  {  
    songCount = 0;

    File root = SD.open(path);
    File file = root.openNextFile();

    while(file && songCount < MAX_SONGS)
    {
        String name = file.name();

        if(!file.isDirectory() && name.endsWith(".mp3"))
        {
            songs[songCount] = String(path) + "/" + name;
            songCount++;
        }

        file = root.openNextFile();
    }

    root.close();
}

void setup() {
  // put your setup code here, to run once:
  Serial.begin(115200);

  // UART communication
  Serial2.begin(115200, SERIAL_8N1, RXD2, TXD2);

  // Initialize SD card
  if(!SD.begin(SD_CS))
  {
    Serial.println("SD Card Mount Failed");
    while(true);
  }

  Serial.println("SD Card Ready");

  // Configure I2S output
  audio.setPinout(I2S_BCLK, I2S_LRC, I2S_DOUT);

  // Volume range 0 - 21
  audio.setVolume(15);

  const char* path = "/music";
  
  analogReadResolution(12);


  
}

void loop() {
  // put your main code here, to run repeatedly:

  audio.loop();

  if(Serial2.available())
  {
    String command = Serial2.readStringUntil('\n');
    if(command == "PLAY")
  {
    playMusic();
  }
  if(command == "STOP")
  {
    audio.stopSong();
    isPlaying = false;
  }
  if(command == "PREV")
  {
    prevMusic();
  }
  if(command == "NEXT")
  {
    nextMusic();
  }
  }

  int raw = analogRead(POT_PIN);
  float normalized = raw / 4095.0;

  smoothed = (alpha * normalized) + ((1 - alpha) * smoothed);

  // Convert to 0–21
  int vol = smoothed * 21;

  audio.setVolume(vol);
  

}

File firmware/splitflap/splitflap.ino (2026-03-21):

#include <WiFi.h>
#include <time.h>
#include <WiFiClientSecure.h>
#include <variables.h>
#include <WebServer.h>

WebServer server(80);

// Function Prototypes
void calibration();
void wifiConnect();
void getTime();
unsigned long getUnixTime();
void UnixConversion();
int dayUpdate = 0;

void setup() 
{
  for(int i = 0; i < 7; i++)
  {
    pinMode(stepPins[i], OUTPUT);
    pinMode(dirPins[i], OUTPUT);
  }

  pinMode(enablePin, OUTPUT);
  pinMode(sleepPin, OUTPUT);

  digitalWrite(enablePin, HIGH); // disabled
  digitalWrite(sleepPin, HIGH); // awake

  setupCalibration();
  wifiConnect();
  getTime();
  displayDayInfo();

  digitalWrite(sleepPin, LOW);
  delay(20000);
  digitalWrite(sleepPin, HIGH);

  displayWeekDay();

  digitalWrite(sleepPin, LOW);
  delay(20000);
  digitalWrite(sleepPin, HIGH);

  displayTime();

  digitalWrite(sleepPin, LOW); // sleep (no current passes)

  server.on("/", handleRoot);
  server.on("/time/now", handleTimeNow);
  server.on("/info/now", handleInfoNow);
  server.on("/displayWord", handleDisplayWord);
  server.on("/play/now", handlePlayNow);
  server.on("/stop/now", handleStopNow);
  server.on("/next/now", handleNextNow);
  server.on("/previous/now", handlePreviousNow);


  Serial.println("IP Address: ")
  Serial.println(WiFi.localIP());
  server.begin();
  Serial.println("HTTP server started");

  Serial2.begin(115200, SERIAL_8N1, 16, 17);
}

void loop()
{
  timeCalculation();
  if(minute4 == 0 && dayUpdate == 0)
  { 
    digitalWrite(sleepPin, HIGH);
    displayDayInfo();
    digitalWrite(sleepPin, LOW);
    delay(10000);
    digitalWrite(sleepPin, HIGH);
    displayWeekDay();
    digitalWrite(sleepPin, LOW);
    delay(5000);
    digitalWrite(sleepPin, HIGH);
    displayWeather()
    digitalWrite(sleepPin, LOW);
    dayUpdate++;
  }
  else if(minute4 != 0 && dayUpdate == 1)
  {
    dayUpdate = 0;
  }
  
  server.handleClient();
}

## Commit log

2026-03-06 Day 9
    [Drum.f3d, Flaps.f3d, Spool Stand.f3z]
2026-03-21 Review Commit
    [BOM Split Flap Device.csv, Full Circuit.kicad_sch, Wiring Schematic.kicad_pcb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]
2026-05-03 Add project documentation for Split Flap Machine
    Documented the creation process of a Split Flap Machine, including design updates, code implementations, and a final BOM list.
